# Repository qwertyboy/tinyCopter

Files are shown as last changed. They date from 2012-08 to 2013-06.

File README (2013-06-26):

tinyCopter v2 - arduino based quadcopter project

Specifications:
	-Atmega328 @ 16MHz
	-ADXL345 Accelerometer and ITG-3200 Gyroscope
	-USB for debugging and updating
	-Reads standard R/C receiver
	-Uses the AeroQuad firmware

----OLD VERSION----

tinyCopter rev C - xmega based quadcopter project

Specifications:
	-xmega32a4u @ 32MHz
	-ADXL345 Accelerometer and ITG-3200 Gyroscope
	-USB for debugging and updating
	-Reads standard R/C receiver

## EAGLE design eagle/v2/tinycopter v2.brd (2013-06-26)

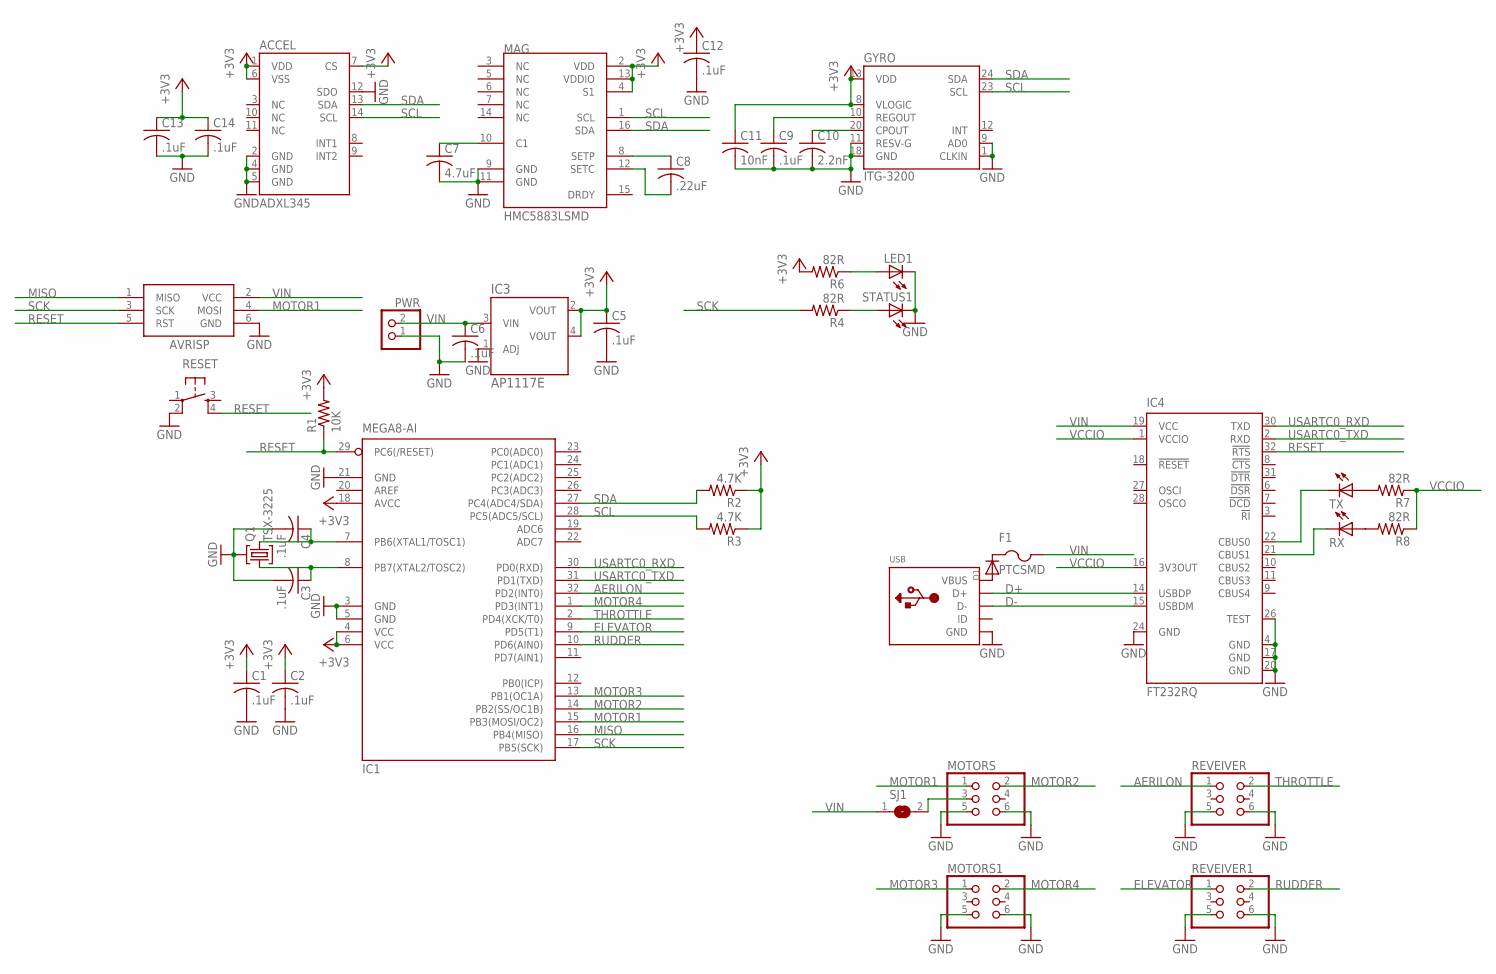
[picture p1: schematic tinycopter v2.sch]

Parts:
ACCEL: ADXL345; LGA14
AVRISP: AVRISP-6; AVRISP
C1, C2, C3, C4, C5, C6, C9, C12, C13, C14: .1uF; C0603
C7: 4.7uF; C0805K
C8: .22uF; C0603
C10: 2.2nF; C0603
C11: 10nF; C0603
D1: DIODESOD-123; SOD-123
F1: PTCSMD; 1812
GYRO: ITG-3200; QFN-24
IC1: MEGA8-AI; TQFP32-08
IC3: AP1117E; SOT223-3
IC4: FT232RQ; QFN32
LED1: LEDCHIP-LED0805; CHIP-LED0805
MAG: HMC5883LSMD; 16LPCC
MOTORS, MOTORS1: PINHD-2X3; 2X03
PWR: JST_2PIN-THM; JST-PH-2-THM
Q1: TSX-3225
R1: 10K; R0603
R2, R3: 4.7K; R0603
R4, R6, R7, R8: 82R; R0603
RESET: TAC_SWITCHSMD; TACTILE_SWITCH_SMD
REVEIVER, REVEIVER1: PINHD-2X3; 2X03
RX: LEDCHIP-LED0805; CHIP-LED0805
SJ1: SJ
STATUS1: LEDCHIP-LED0805; CHIP-LED0805
TX: LEDCHIP-LED0805; CHIP-LED0805
USB: USBMINIB; USB-MINIB

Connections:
+3V3: ACCEL.1 (VDD), ACCEL.6 (VSS), ACCEL.7 (CS), C1.1, C2.1, C5.1, C11.1, C12.1, C13.1, C14.1, GYRO.8 (VLOGIC), GYRO.13 (VDD), IC1.4 (VCC), IC1.6 (VCC), IC1.18 (AVCC), IC3.2 (VOUT), IC3.4 (VOUT), MAG.2 (VDD), MAG.4 (S1), MAG.13 (VDDIO), R1.2, R2.1, R3.1, R6.2
AERILON: IC1.32 (PD2(INT0)), REVEIVER.1
D+: IC4.14 (USBDP), USB.D+
D-: IC4.15 (USBDM), USB.D-
ELEVATOR: IC1.9 (PD5(T1)), REVEIVER1.1
GND: ACCEL.2 (GND), ACCEL.4 (GND), ACCEL.5 (GND), ACCEL.12 (SDO), AVRISP.6 (GND), C1.2, C2.2, C3.2, C4.2, C5.2, C6.2, C7.2, C9.2, C10.2, C11.2, C12.2, C13.2, C14.2, GYRO.1 (CLKIN), GYRO.9 (AD0), GYRO.11 (RESV-G), GYRO.18 (GND), IC1.3 (GND), IC1.5 (GND), IC1.21 (GND), IC3.1 (ADJ), IC4.4 (GND), IC4.17 (GND), IC4.20 (GND), IC4.24 (GND), IC4.26 (TEST), LED1.C, MAG.9 (GND), MAG.11 (GND), MOTORS.5, MOTORS.6, MOTORS1.5, MOTORS1.6, PWR.1 (2), Q1.2 (3), Q1.4 (3), RESET.2, REVEIVER.5, REVEIVER.6, REVEIVER1.5, REVEIVER1.6, STATUS1.C, USB.GND
MISO: AVRISP.1 (MISO), IC1.16 (PB4(MISO))
MOTOR1: AVRISP.4 (MOSI), IC1.15 (PB3(MOSI/OC2)), MOTORS.1
MOTOR2: IC1.14 (PB2(SS/OC1B)), MOTORS.2
MOTOR3: IC1.13 (PB1(OC1A)), MOTORS1.1
MOTOR4: IC1.1 (PD3(INT1)), MOTORS1.2
unnamed: C4.1, IC1.7 (PB6(XTAL1/TOSC1)), Q1.3 (2)
unnamed: C3.1, IC1.8 (PB7(XTAL2/TOSC2)), Q1.1
unnamed: R4.1, STATUS1.A
unnamed: C10.1, GYRO.20 (CPOUT)
unnamed: C7.1, MAG.10 (C1)
unnamed: C8.1, MAG.8 (SETP)
unnamed: LED1.A, R6.1
unnamed: C8.2, MAG.12 (SETC)
unnamed: C9.1, GYRO.10 (REGOUT)
unnamed: IC4.22 (CBUS0), TX.C
unnamed: IC4.21 (CBUS1), RX.C
unnamed: R7.2, TX.A
unnamed: D1.A, USB.VBUS
unnamed: R8.2, RX.A
unnamed: D1.C, F1.1
unnamed: MOTORS.3, SJ1.2
RESET: AVRISP.5 (RST), IC1.29 (PC6(/RESET)), IC4.32 (!RTS), R1.1, RESET.4
RUDDER: IC1.10 (PD6(AIN0)), REVEIVER1.2
SCK: AVRISP.3 (SCK), IC1.17 (PB5(SCK)), R4.2
SCL: ACCEL.14 (SCL), GYRO.23 (SCL), IC1.28 (PC5(ADC5/SCL)), MAG.1 (SCL), R3.2
SDA: ACCEL.13 (SDA), GYRO.24 (SDA), IC1.27 (PC4(ADC4/SDA)), MAG.16 (SDA), R2.2
THROTTLE: IC1.2 (PD4(XCK/T0)), REVEIVER.2
USARTC0_RXD: IC1.30 (PD0(RXD)), IC4.30 (TXD)
USARTC0_TXD: IC1.31 (PD1(TXD)), IC4.2 (RXD)
VCCIO: IC4.1 (VCCIO), IC4.16 (3V3OUT), R7.1, R8.1
VIN: AVRISP.2 (VCC), C6.1, F1.2, IC3.3 (VIN), IC4.19 (VCC), PWR.2 (1), SJ1.1

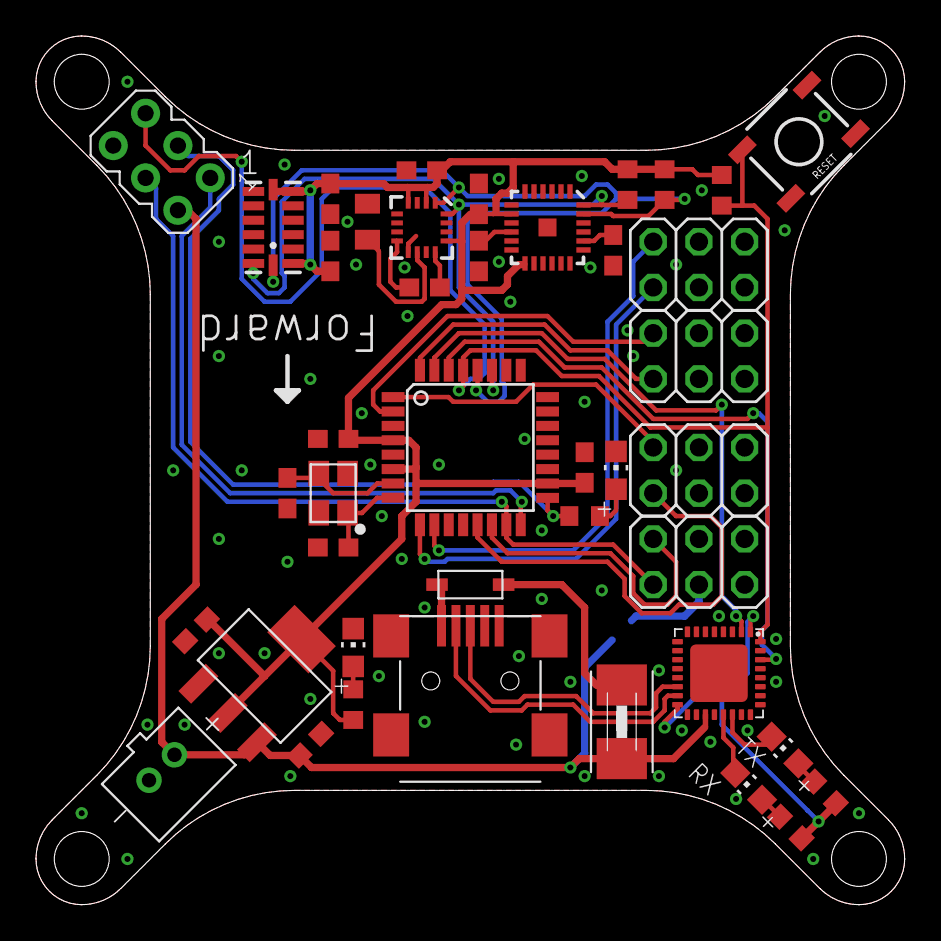
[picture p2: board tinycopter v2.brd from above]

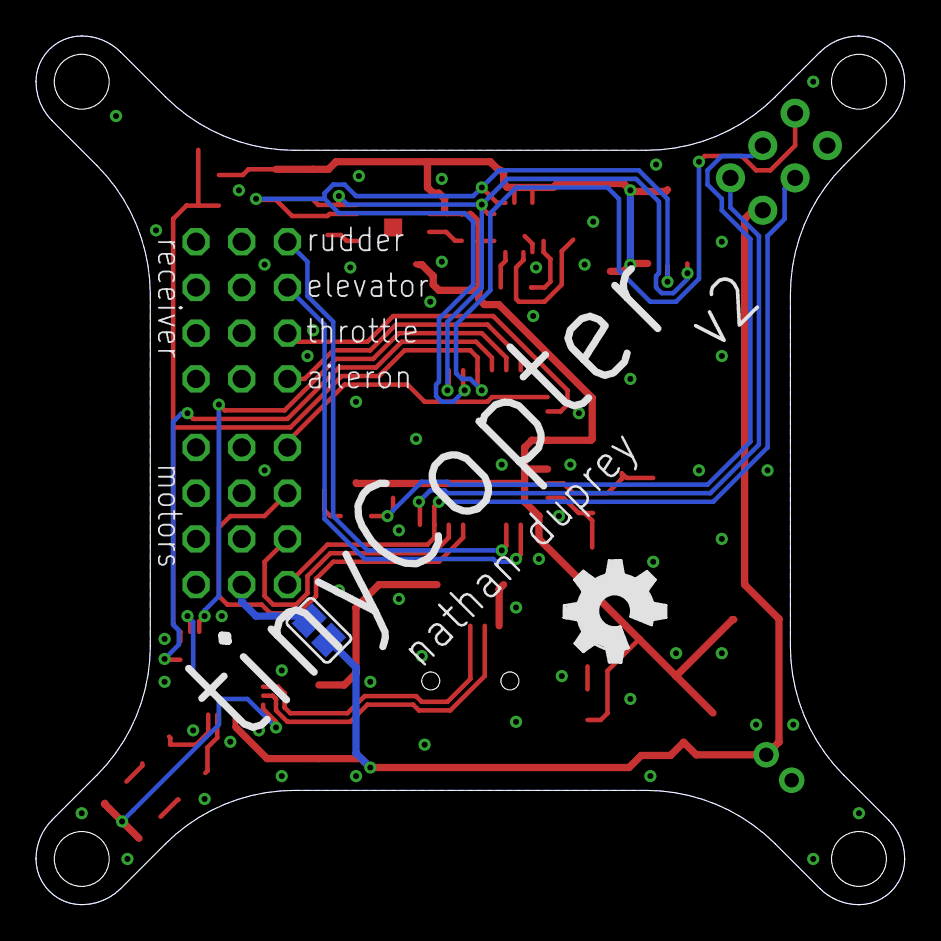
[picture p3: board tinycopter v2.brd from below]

Board: 2 copper layers, 48.3 x 48.3 mm, 44 parts (2 on the bottom side), 37 nets.

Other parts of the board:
U$1: OSHW_FILLX200_NOTEXT

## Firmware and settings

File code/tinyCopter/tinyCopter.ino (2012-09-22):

/////////////////////////////////////////////////////////
//					               //
//	     tinyCopter v1 - August 2012               //
//						       //
//	   www.qwertyboydesign.wordpress.com           //
//        youtube.com/user/qwertyboy1234567899         //
//						       //
/////////////////////////////////////////////////////////
//   _   _              _____            _             //
//  | | (_)            / ____|          | |            //
//  | |_ _ _ __  _   _| |     ___  _ __ | |_ ___ _ __  //
//  | __| | '_ \| | | | |    / _ \| '_ \| __/ _ \ '__| //
//  | |_| | | | | |_| | |___| (_) | |_) | ||  __/ |    //
//   \__|_|_| |_|\__, |\_____\___/| .__/ \__\___|_|    //
//                __/ |           | |                  //
// Nathan Duprey |___/            |_|        Version 1 //
//						       //
/////////////////////////////////////////////////////////


#include "Wire.h"      //I2Cdevlib depends on the Wire library
#include "I2Cdev.h"    //General operations for the sensor libraries
#include "ADXL345.h"   //ADXL345 library
#include "ITG3200.h"   //ITG-3200 library
#include "ascii_art.h" //Library for custom ASCII art
//#include "motors.h"    //Library for motor control
//#include "receiver.h"  //Library for reading receiver

#include "C:\Documents and Settings\Nathan\arduino-1.0.1-rc2-xmegaduino-beta4-original\libraries\AVR1305\pmic_driver.c"
#include "C:\Documents and Settings\Nathan\arduino-1.0.1-rc2-xmegaduino-beta4-original\libraries\AVR1305\pmic_driver.h"
#include "C:\Documents and Settings\Nathan\arduino-1.0.1-rc2-xmegaduino-beta4-original\libraries\AVR1306\TC_driver.c"
#include "C:\Documents and Settings\Nathan\arduino-1.0.1-rc2-xmegaduino-beta4-original\libraries\AVR1306\TC_driver.h"

ADXL345 accel;         //Using default addresses for both devices
ITG3200 gyro;

int accel_xout, accel_yout, accel_zout;  //Containers for raw acceleration data
int gyro_xout, gyro_yout, gyro_zout;     //Containers for raw gyroscope data

#define status_led1 13 //Pins for the status LEDs
#define status_led2 12

#define MOTOR1 0
#define MOTOR2 0
#define MOTOR3 0
#define MOTOR4 0

////////////////Target Angle Calculations////////////////

int roll_input;
int pitch_input;
int throttle_input;
int yaw_input;

#define ROLL_MIN 582
#define ROLL_MID 756
#define ROLL_MAX 950
#define PITCH_MIN 587
#define PITCH_MID 747
#define PITCH_MAX 926
#define THROTTLE_MIN 565
#define THROTTLE_MID 738
#define THROTTLE_THRESHOLD 600
#define THROTTLE_MAX 923
#define YAW_MIN 560
#define YAW_MID 750
#define YAW_MAX 921

#define XANGLE_RANGE 30
#define YANGLE_RANGE 30
#define ZRATE_RANGE 30

float TARGET_ZRATE = 0.0;
float throttle = 0.0;
float TARGET_XANGLE = 0.0;
float TARGET_YANGLE = 0.0;

float ACCEL_XANGLE;
float ACCEL_YANGLE;

float GYRO_XRATE;
float GYRO_YRATE;
float GYRO_ZRATE;
float GYRO_XANGLE;
float GYRO_YANGLE;
float GYRO_ZANGLE;

float filter_xterm[3] = {0,0,0};
float filter_yterm[3] = {0,0,0};
#define timeConstant 0.1
float COMPLEMENTARY_XANGLE;
float COMPLEMENTARY_YANGLE;

///////////////////////PID Control///////////////////////

float KP;
float KD;
float KI;
float ZKP;
float ZKD;

float XERROR;
float YERROR;
float ZERROR;

float PREVIOUS_XERROR = 0;
float PREVIOUS_YERROR = 0;
float PREVIOUS_ZERROR = 0;

float XDIFFERENTIAL = 0;
float YDIFFERENTIAL = 0;
float ZDIFFERENTIAL = 0;

float XINTEGRAL;
float YINTEGRAL;

float PID_XOUTPUT;
float PID_YOUTPUT;
float PID_ZOUTPUT;

//////////////////////Motor Control//////////////////////

#define MOTOR_MIN 510
#define MOTOR_MAX 950
#define MOTOR_RANGE 440

float motor1_speed;
float motor2_speed;
float motor3_speed;
float motor4_speed;

/////////////////////////////////////////////////////////

void setup(){
  pinMode(status_led1, OUTPUT);  //Status LEDs are outputs
  pinMode(status_led2, OUTPUT);
  
  //pinMode(MOTOR1, OUTPUT);  //Motors are outputs
  //pinMode(MOTOR2, OUTPUT);
  //pinMode(MOTOR3, OUTPUT);
  //pinMode(MOTOR4, OUTPUT);
  
  Wire.begin();       //We are using TWIC on an xmega A4
  
  Serial.begin(38400); //Start serial for debugging and such
  print_tinyCopter_ASCII();
  
  //Now we are going to initialize our sensors
  Serial.println("Initializing sensors...");
  accel.initialize();
  //accel.setRange(0x1);  // +/-4g range
  gyro.initialize();
  
  delay(100);          //Wait a little bit for things to settle
  
  //We are going to test the connections to our sensors
  Serial.println("Testing sensors...");
  
  bool accel_test_status = accel.testConnection();
  //byte accel_range = accel.getRange();
  delay(100);           //I think we need to wait for the transaction to take place before starting the next one
  bool gyro_test_status = gyro.testConnection();
  
  switch(accel_test_status){
    case true:
    Serial.println("Accelerometer all good!");
    //Serial.print("Range: ");
    //Serial.println(accel_range);
    break;
    
    case false:
    Serial.println("Accelerometer is broken!");
    while(1){
      digitalWrite(status_led1, HIGH);
      delay(100);
      digitalWrite(status_led1, LOW);
      delay(100);
    }
    break;
  }
  
  switch(gyro_test_status){
    case true:
    Serial.println("Gyroscope all good!");
    Serial.println("");
    break;
    
    case false:
    Serial.println("Gyroscope is broken!");
    while(1){
      digitalWrite(status_led2, HIGH);
      delay(100);
      digitalWrite(status_led2, LOW);
      delay(100);
    }
    break;
  }
  
  cli();
  setup_motorPWM_timer();
  setup_receiverCapture_timer();
  //setup_mainloop_timer();
  sei();
}

void loop(){
  getTargetAngles();
  getGyroRates();
  getAccelAngles();
  
  dataFilter();
  updatePID();
  
  updateMotors();
  Serial.println(GYRO_XANGLE);
}





//Function to set up interrupt for the main control loop
void setup_mainloop_timer(){
  TC_SetPeriod(&TCD1, 0x270F);                        //Set period register at 9999 to create 400Hz interrupt 0x270F
  TC1_ConfigClockSource(&TCD1, TC_CLKSEL_DIV8_gc);    //Use F_CPU/8 as timer clock
  TC1_SetOverflowIntLevel(&TCD1, TC_OVFINTLVL_HI_gc); //Enable high-level interrupt on overflow
  
  //TCD1.CTRLA = (1<<0x08);      //Set timer E0 to use F_CPU/8 as clock - figure out why this doesn't work
  //TCD1.PER = 0x270F;            //Set period register at 9999 to cause an interrupt at 400Hz - this works
  //TCD1.INTCTRLA |= (1<<0X03);   //Set up timer as highest level interrupt (besides NMI) - figure out why this doesn't work
  //PMIC_EnableHighLevel();
  
  //ISR(TCD1_OVF_vect){       //This is what the ISR funtion should look like
  //}
  Serial.println("Main loop timer set up!");
}





//Function to set up interrupt for MOTOR1 PWM
void setup_motorPWM_timer(){
  PORTD.DIRSET = 0xFF;                               //Set PORTD pins as outputs. I thought the compare channels
                                                     //automatically did this...
  
  TC_SetPeriod(&TCD0, 0x270F);                       //Set period register at 9999 to create 50Hz(20ms) interrupt
  TC0_ConfigClockSource(&TCD0, TC_CLKSEL_DIV64_gc);  //Use F_CPU/64 as timer clock
  TC0_ConfigWGM(&TCD0, TC_WGMODE_SS_gc);             //Set timer for single slope PWM
  
  TC0_EnableCCChannels(&TCD0, TC0_CCAEN_bm);         //Enable compare channel A/MOTOR1
  TC0_EnableCCChannels(&TCD0, TC0_CCBEN_bm);         //Enable compare channel B/MOTOR2
  TC0_EnableCCChannels(&TCD0, TC0_CCCEN_bm);         //Enable compare channel C/MOTOR3
  TC0_EnableCCChannels(&TCD0, TC0_CCDEN_bm);         //Enable compare channel D/MOTOR4
  
  TC_SetCompareA(&TCD0, 0x1FE);                          //Set the compare register at 0 to start
  TC_SetCompareB(&TCD0, 0x1FE);                          //Set the compare register at 0 to start
  TC_SetCompareC(&TCD0, 0x1FE);                          //Set the compare register at 0 to start
  TC_SetCompareD(&TCD0, 0x1FE);                          //Set the compare register at 0 to start
                                                     //0x1FE(510) is minimum, 3FC(1020) is maximum(so far)
  
  Serial.println("Motor PWM timer set up!");
}





void setup_receiverCapture_timer(){  
  PORTE.DIRCLR = 0xFF;                              //Configure PE0-3 for input
  
  PORTE.PIN0CTRL = PORT_ISC_BOTHEDGES_gc;           //Configure PE0 for triggering on both edges
  PORTE.PIN1CTRL = PORT_ISC_BOTHEDGES_gc;           //Configure PE1 for triggering on both edges
  PORTE.PIN2CTRL = PORT_ISC_BOTHEDGES_gc;           //Configure PE2 for triggering on both edges
  PORTE.PIN3CTRL = PORT_ISC_BOTHEDGES_gc;           //Configure PE3 for triggering on both edges
  
  TC_SetPeriod(&TCE0, 0x7FFF);                      //Clear MSB of period register for detecting edge polarity 0x7FFF
  TC0_ConfigClockSource(&TCE0, TC_CLKSEL_DIV64_gc); //Use F_CPU/64 for a resolution of 2us
  
  TC0_EnableCCChannels(&TCE0, TC0_CCAEN_bm);        //Enable capture channel A
  TC0_EnableCCChannels(&TCE0, TC0_CCBEN_bm);        //Enable capture channel B
  TC0_EnableCCChannels(&TCE0, TC0_CCCEN_bm);        //Enable capture channel C
  TC0_EnableCCChannels(&TCE0, TC0_CCDEN_bm);        //Enable capture channel D

  EVSYS.CH0MUX = EVSYS_CHMUX_PORTE_PIN0_gc;         //Select PE0 as input to event channel 0
  EVSYS.CH1MUX = EVSYS_CHMUX_PORTE_PIN1_gc;         //Select PE1 as input to event channel 1
  EVSYS.CH2MUX = EVSYS_CHMUX_PORTE_PIN2_gc;         //Select PE2 as input to event channel 2
  EVSYS.CH3MUX = EVSYS_CHMUX_PORTE_PIN3_gc;         //Select PE3 as input to event channel 3
  
  TCE0.CTRLD |= TC_EVACT_PW_gc;                      //Enable pulse width capture event
  TCE0.CTRLD |= TC_EVSEL_CH0_gc;                     //Set event source to channel 0. still a bit confused here
  
  Serial.println("Receiver capture timer set up!");
}





//Main loop interrupt
volatile int pulse_widthA = 0;
volatile int pulse_widthB = 0;
volatile int pulse_widthC = 0;
volatile int pulse_widthD = 0;

volatile unsigned int counter = 0;
volatile int state = 0;

//400Hz Control loop
//ISR(TCD1_OVF_vect){
  //getTargetAngles();
  //cli();
  
  //getGyroRates();
  //getAccelAngles();
  
  //dataFilter();
  
  //updatePID();
  
  //sei();
  //updateMotors();
//  accel.getAcceleration(&accel_xout, &accel_yout, &accel_zout);
//  Serial.println("hi");
//}





//Capture channel A
//volatile int pulse_width = 0;
//ISR(TCE0_CCD_vect){
//  pulse_width = TCE0.CCD;
//  Serial.println(pulse_width);
//}

//Read RC receiver and get target angles
void getTargetAngles(){
  
  yaw_input = TCE0.CCD;
  TARGET_ZRATE = ZRATE_RANGE * (yaw_input - YAW_MID)/(YAW_MAX - YAW_MIN);
  
  throttle_input = TCE0.CCC;
  if(throttle_input <= THROTTLE_THRESHOLD){
    throttle = 0.0;
  }else{
    throttle = (float)(throttle_input - THROTTLE_MIN)/(THROTTLE_MAX - THROTTLE_MIN);
  }
  
  roll_input = TCE0.CCA;
  TARGET_XANGLE = XANGLE_RANGE * (roll_input - ROLL_MID)/(ROLL_MAX - ROLL_MIN);
  
  pitch_input = TCE0.CCB;
  TARGET_YANGLE = YANGLE_RANGE *(float)((float)(pitch_input - PITCH_MID)/(PITCH_MAX - PITCH_MIN));
}

//Read accelerometer and calculate angles
void getAccelAngles(){
  accel.getAcceleration(&accel_xout, &accel_yout, &accel_zout);
  
  ACCEL_XANGLE = 57.295 * atan(accel_yout / sqrt(pow(accel_zout, 2) + pow(accel_xout, 2)));
  ACCEL_YANGLE = 57.295 * atan(-accel_xout / sqrt(pow(accel_zout, 2) + pow(accel_yout, 2)));
}

//Read gyroscope and calculate angles
void getGyroRates(){
  gyro.getRotation(&gyro_xout, &gyro_yout, &gyro_zout);
  
  GYRO_XRATE = (float)gyro_xout / 14.375;
  GYRO_YRATE = (float)gyro_yout / 14.375;
  GYRO_ZRATE = (float)gyro_zout / 14.375;
  
  GYRO_XANGLE += GYRO_XRATE * 0.0025;
  GYRO_YANGLE += GYRO_YRATE * 0.0025;
  GYRO_ZANGLE += GYRO_ZRATE * 0.0025;
}

//2nd order complementary filter`
void dataFilter(){
  filter_xterm[0] = (ACCEL_XANGLE - COMPLEMENTARY_XANGLE) * timeConstant * timeConstant;
  filter_yterm[0] = (ACCEL_YANGLE - COMPLEMENTARY_YANGLE) * timeConstant * timeConstant;
  
  filter_xterm[2] = (0.0025 * filter_xterm[0]) + filter_xterm[2];
  filter_yterm[2] = (0.0025 * filter_yterm[0]) + filter_yterm[2];
  
  filter_xterm[1] = filter_xterm[2] + (ACCEL_XANGLE - COMPLEMENTARY_XANGLE) * 2 * timeConstant + GYRO_XRATE;
  filter_yterm[1] = filter_yterm[2] + (ACCEL_YANGLE - COMPLEMENTARY_YANGLE) * 2 * timeConstant + GYRO_YRATE;
  
  COMPLEMENTARY_XANGLE = (0.0025 * filter_xterm[1]) + COMPLEMENTARY_XANGLE;
  COMPLEMENTARY_YANGLE = (0.0025 * filter_yterm[1]) + COMPLEMENTARY_YANGLE;
}

//PID algorithm
void updatePID(){
  PREVIOUS_XERROR = XERROR;
  PREVIOUS_YERROR = YERROR;
  PREVIOUS_ZERROR = ZERROR;

  XERROR = TARGET_XANGLE - COMPLEMENTARY_XANGLE;
  YERROR = TARGET_YANGLE - COMPLEMENTARY_YANGLE;
  ZERROR = TARGET_ZRATE - GYRO_ZRATE;

  //XDIFFERENTIAL = (XERROR - PREVIOUS_XERROR)/dt;	
  //YDIFFERENTIAL = (YERROR - PREVIOUS_YERROR)/dt;
  //ZDIFFERENTIAL = (ZERROR - PREVIOUS_ZERROR)/dt;

  XDIFFERENTIAL = -GYRO_XRATE;
  YDIFFERENTIAL = -GYRO_YRATE;
  ZDIFFERENTIAL = -GYRO_ZRATE;

  XINTEGRAL += XERROR * 0.0025;
  YINTEGRAL += YERROR * 0.0025;

  if(XINTEGRAL > 0.5) {XINTEGRAL = 0.5;}
  else if(XINTEGRAL < -0.5) {XINTEGRAL = -0.5;}
  if(YINTEGRAL > 0.5) {YINTEGRAL = 0.5;}
  else if(YINTEGRAL < -0.5) {YINTEGRAL = -0.5;}

  PID_XOUTPUT = XERROR * KP + XDIFFERENTIAL * KD + XINTEGRAL * KI;
  PID_YOUTPUT = YERROR * KP + YDIFFERENTIAL * KD + YINTEGRAL * KI;
  PID_ZOUTPUT = ZERROR * ZKP; + ZDIFFERENTIAL * ZKD;
  if(PID_ZOUTPUT > 1000){PID_ZOUTPUT = 1000;}
  else if (PID_ZOUTPUT < -1000){PID_ZOUTPUT = -1000;}	
}

void updateMotors(){
  if(throttle == 0.0){
    TC_SetCompareA(&TCD0, 0x1FE);                          //Set the compare register at 510
    TC_SetCompareB(&TCD0, 0x1FE);                          //Set the compare register at 510
    TC_SetCompareC(&TCD0, 0x1FE);                          //Set the compare register at 510
    TC_SetCompareD(&TCD0, 0x1FE);                          //Set the compare register at 510
  }else{
    motor1_speed = 0.7071 * PID_XOUTPUT + -0.7071 * PID_YOUTPUT + PID_ZOUTPUT + MOTOR_MIN + MOTOR_RANGE * throttle;
    motor2_speed = 0.7071 * PID_XOUTPUT + 0.7071 * PID_YOUTPUT - PID_ZOUTPUT + MOTOR_MIN + MOTOR_RANGE * throttle;
    motor3_speed = -0.7071 * PID_XOUTPUT + 0.7071 * PID_YOUTPUT + PID_ZOUTPUT + MOTOR_MIN + MOTOR_RANGE * throttle;
    motor4_speed = -0.7071 * PID_XOUTPUT + -0.7071 * PID_YOUTPUT - PID_ZOUTPUT + MOTOR_MIN + MOTOR_RANGE * throttle;
    
    if(motor1_speed > MOTOR_MAX)  {motor1_speed = MOTOR_MAX;}
    if(motor2_speed > MOTOR_MAX)  {motor2_speed = MOTOR_MAX;}
    if(motor3_speed > MOTOR_MAX)  {motor3_speed = MOTOR_MAX;}
    if(motor4_speed > MOTOR_MAX)  {motor4_speed = MOTOR_MAX;}
    
    if(motor1_speed < MOTOR_MIN)  {motor1_speed = MOTOR_MIN;}
    if(motor2_speed < MOTOR_MIN)  {motor2_speed = MOTOR_MIN;}
    if(motor3_speed < MOTOR_MIN)  {motor3_speed = MOTOR_MIN;}
    if(motor4_speed < MOTOR_MIN)  {motor4_speed = MOTOR_MIN;}
    
    TC_SetCompareA(&TCD0, motor1_speed);
    TC_SetCompareB(&TCD0, motor2_speed);
    TC_SetCompareC(&TCD0, motor3_speed);
    TC_SetCompareD(&TCD0, motor4_speed);
  }
}

void calibrateESC(){
  int x = 0;
  
  for(x = 0; x < 400; x++){
    TC_SetCompareA(&TCD0, MOTOR_MAX);
    TC_SetCompareB(&TCD0, MOTOR_MAX);
    TC_SetCompareC(&TCD0, MOTOR_MAX);
    TC_SetCompareD(&TCD0, MOTOR_MAX);
    
    delayMicroseconds(250);
  }
  
  for(x = 0; x < 400; x++){
    TC_SetCompareA(&TCD0, MOTOR_MIN);
    TC_SetCompareB(&TCD0, MOTOR_MIN);
    TC_SetCompareC(&TCD0, MOTOR_MIN);
    TC_SetCompareD(&TCD0, MOTOR_MIN);
    
    delayMicroseconds(250);
  }
}

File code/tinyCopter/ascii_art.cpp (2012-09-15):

////////////////////////////////////////////////////////////////////////////
//                  _ _                       _                           //
//                 (_|_)                     | |                          //
//    __ _ ___  ___ _ _             __ _ _ __| |_        ___ _ __  _ __   //
//   / _` / __|/ __| | |           / _` | '__| __|      / __| '_ \| '_ \  //
//  | (_| \__ \ (__| | |          | (_| | |  | |_   _  | (__| |_) | |_) | //
//   \__,_|___/\___|_|_|           \__,_|_|   \__| (_)  \___| .__/| .__/  //
//                        ______                            | |   | |     //
//                       |______|                           |_|   |_|     //
////////////////////////////////////////////////////////////////////////////
#include "Arduino.h"
#include "ascii_art.h"





/////////////////////////////////////////////////////////
//   _   _              _____            _             //
//  | | (_)            / ____|          | |            //
//  | |_ _ _ __  _   _| |     ___  _ __ | |_ ___ _ __  //
//  | __| | '_ \| | | | |    / _ \| '_ \| __/ _ \ '__| //
//  | |_| | | | | |_| | |___| (_) | |_) | ||  __/ |    //
//   \__|_|_| |_|\__, |\_____\___/| .__/ \__\___|_|    //
//                __/ |           | |                  //
// Nathan Duprey |___/            |_|        Version 1 //
/////////////////////////////////////////////////////////
void print_tinyCopter_ASCII(){
  //Cool ASCII art banner
  Serial.println("  _   _              _____            _            ");
  Serial.println(" | | (_)            / ____|          | |           ");
  Serial.println(" | |_ _ _ __  _   _| |     ___  _ __ | |_ ___ _ __ ");
  Serial.print(" | __| | '_ ");
  Serial.write(0x5C);
  Serial.print("| | | | |    / _ ");
  Serial.write(0x5C);
  Serial.print("| '_ ");
  Serial.write(0x5C);
  Serial.print("| __/ _ ");
  Serial.write(0x5C);
  Serial.println(" '__|");
  Serial.println(" | |_| | | | | |_| | |___| (_) | |_) | ||  __/ |   ");
  Serial.print("  ");
  Serial.write(0x5C);
  Serial.print("__|_|_| |_|");
  Serial.write(0x5C);
  Serial.print("__, |");
  Serial.write(0x5C);
  Serial.print("_____");
  Serial.write(0x5C);
  Serial.print("___/| .__/ ");
  Serial.write(0x5C);
  Serial.print("__");
  Serial.write(0x5C);
  Serial.println("___|_|   ");
  Serial.println("               __/ |           | |                 ");
  Serial.println("Nathan Duprey |___/            |_|        Version 1");
  Serial.println("");
}

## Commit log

2012-05-11 Added EAGLE schematic and layout files
    [xmega.brd, xmega.sch]
2012-05-11 Moved EAGLE files for the mainboard
    [xmega.brd, xmega.sch]
2012-05-11 Moving things around
    [xmega.brd, xmega.sch]
2012-05-11 Added EAGLE schematic and layout files for tx/rx.
    [main.brd, main.sch, usb.brd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]
2012-08-02 Added revision C design and moved the rev B stuff
    [main_c.brd, main_c.sch, xmega.brd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]
2012-08-02 Deleted folder
    [xmega.brd, xmega.sch]
2012-08-05 Tweaked the board a bit
    [main_c.brd]
2012-09-15 Lots of progress on code. PWM works, working on input capture
2013-06-26 removed tx_rx folder, added eagle files for (hopefully) final version
    [main.brd, main.sch, tinycopter v2.brd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]
